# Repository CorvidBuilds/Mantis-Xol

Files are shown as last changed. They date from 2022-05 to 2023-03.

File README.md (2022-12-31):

# Hey! You should be looking at the [Armchair Engineering fork](https://github.com/Armchair-Engineering/Mantis-Xol) for the most up-to-date version!

# Mantis Xol 2


## Description
Originally a project to slap 5020 blower fans onto Mantis, this toolhead variant started as an attempt to improve parts cooling, spurred on by Derpimus' noted cooling woes on his DOOMCube. After finding that the 5020s were just plain too fat to fit without looking like a standard Ender 3 Thingiverse special, I abandoned the large fan dream in favor of better cooling efficiency and lighter weight. This new and improved dream was also corrupted by my then budding and now all-consuming love for worm gears.

## New Features for Xol 2
 - Cooler: Still a little ugly but better
 - Lighter: 260g-ish for Sherpa Mini
 - Rigid-er: I want to throw this thing across the room
 - DropEffect × Phaetus XG support 
 - Revo Voron Support
 - Support for MattTheBaker's Beacon and VoronDesign's Tap

#### Features:
 - Better airflow than Stealthburner (6-7 CFM through short ducts vs 4.6-5.2 CFM through long ducts)
 - Improved resonance management compared to Mantis 5015
 - Support for Sherpa Mini-pattern extruder mounting as well as Annex Engineering's **Double Folded Ascender** worm gear extruder
 - Support for JosAr's Klicky, VinnyCordeiro and WhoppingPochard's PCB Klicky, and Nionio6915's Euclid
 
#### Future Development (No ETA):
 - Bracing for PCB mounts
 - Quickdraw 2 support
 - Update DFA Bottom to latest version for slightly better heatset quality of life
 - Port nozzle LEDs to Xol 2
 - Port MMU sensor support to Xol 2
 - Confirm fitment for MattTheBaker's Beacon

## Build Notes:
This toolhead might require other modifications to retain full functionality of your printer. 
 - All test machines used for this mod had Rama's front idlers which have a much lower profile compared to stock Voron front idlers. The fan assemblies might conflict and reduce usable X travel.
 - The Klicky Probe carriage that was adapted was originally designed for the Dragon hotend. You'll need to use a taller probe body to reach the bed such as the one used by [Unklicky BFP](https://github.com/majarspeed/Unklicky). *This isn't an issue for Euclid or PCB Klicky*.
## Bill of Materials 
|Item|Count|Note|
|----|-|--|
|Rapido or XG|1|
|4010 24v blower fans|2|Add Polulu 3796 if you want the fancy 12v Deltas|
|2510 24v axial fan|1|
|M2x8 SHCS|2|
|M2x12 SHCS|4|
|M2x20 SHCS|2|
|M2.5x20 SHCS|4|
|m3x6 BHCS|7|
|m3x8 BHCS|7|
|m3x20 SHCS|2|
|M2 Heatset 4L x 3.5 OD|11|
|M3 Heatset "Standard"|10|
|D2F-5L Microswitch|1|
|M2x8 or M2x10 Self-Tapping|1|Optionally 1 more M2 heatset and an M2x8 SHCS|
|6x3 magnets|3|
|ZIP TIES||
## Changelog
### 29 November 2022 - Beacon Support
- Release Day means Beacon Support. Find it in the Experimental folder.
### 27 November 2022 - Tap Support
- Release Day means Tap Support. Find it in the Experimental folder.
### 22 November 2022 -Revo Voron
- Added support for Revo Voron with the Sherpa Mini Hotend mount
### 10 November 2022 - Shiny shiny
- Added nozzle LED support. Find it in the Experimental folder.
### 23 October 2022
### 3 October 2022 - Xol 2
- Improved aesthetics
- Downsized HE fan to 2510
- No more self-tapping screws
- Added front brace for Sherpa Mini
- New ducts for Tridents with lead screws
- Miscellaneous printability improvements
### 3 Aug 2022 - Xol with Boots
- Added MGN9H carriages for PCB Klicky
- Added additional stabilization for ducts. Ideally, these are fastened with 2x M2x20 and M2 heatset inserts.


## Acknowledgement
[Long/Mandryd](https://github.com/mandryd/VoronUsers/tree/master/printer_mods/Long/Mantis_Dual_5015) for the Mantis toolhead.<br/>
[TheWarolf](https://github.com/TheWarolf/Voron-Personal-Mods/tree/main/V2/Long_Mantis_Toolhead) for the ERCF sensorized Hotend Mount.<br/>
[Derpimus](https://github.com/lraithel15133) for the exegesis, some CAD work, feedback, and just being a rad dude.<br/>
[KayosMaker](https://github.com/KayosMaker) for the MGN12 Klicky X-Carriage and CAN board mounts and spacers.<br/>
[JosAr](https://github.com/jlas1/Klicky-Probe) for Klicky.<br/>
[WhoppingPochard](https://github.com/tanaes) and [VinnyCordeiro](https://github.com/VinnyCordeiro/) for PCB Klicky.<br/>
[Nionio6915](https://github.com/nionio6915/Euclid_Probe) for Euclid. <br/>
[VoronDesign](https://github.com/VoronDesign) for this particular CoreXY flavor.<br/>
[AnnexEngineering](https://github.com/Annex-Engineering) for the Sherpa Mini and Double Folded Ascender extruders, and the K3 that influenced the air management of the ducts. And also for giving access to an early revision of the new DFA so it could be adapted for this toolhead.<br/>
[Clee](https://github.com/clee), you know what you did.

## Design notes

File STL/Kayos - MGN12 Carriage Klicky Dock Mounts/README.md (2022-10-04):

The Klicky dock and mount can be found in the MantisUsermods repo [here.](https://github.com/mandryd/MantisUsermods/tree/main/Usermods/KayosMaker/MGN12_Klicky/STLs)

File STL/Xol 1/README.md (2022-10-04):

# Mantis Xol 


## Description
Originally a project to slap 5020 blower fans onto Mantis, this toolhead variant started as an attempt to improve parts cooling, spurred on by Derpimus' noted cooling woes on his DOOMCube. After finding that the 5020s were just plain too fat to fit without looking like a standard Ender 3 Thingiverse special, I abandoned the large fan dream in favor of better cooling efficiency and lighter weight. This new and improved dream was also corrupted by my then budding and now all-consuming love for worm gears.

#### Features:
 - Lighter weight (285g Sherpa Mini/300g DFA vs Stealthburner's 430g)
 - Better airflow than Stealthburner (6-7 CFM through short ducts vs 4.6-5.2 CFM through long ducts)
 - Improved resonance management compared to Mantis 5015
 - Support for Sherpa Mini-pattern extruder mounting as well as Annex Engineering's **Double Folded Ascender** worm gear extruder
 - Support for JosAr's Klicky, VinnyCordeiro and WhoppingPochard's PCB Klicky, and Nionio6915's Euclid
 - Nozzle LEDs. They're not the best but they're there.
 
#### Future Development (No ETA):
 - Bracing for PCB mounts
 - Rev 2 for ducts since the current version punishes curling too harshly and might be too low for some nozzles
 - Quickdraw 2 support
 - Update DFA Bottom to latest version for slightly better heatset quality of life
 - Revo support


## Note:
I'm not the owner of some of the STLs in this repo. The rightful owners are included in the filenames and these files will be removed in favor of a readme with links to their origin instead.
## Build Notes:
This toolhead might require other modifications to retain full functionality of your printer. 
 - Both test machines used for this mod had Rama's front idlers which have a much lower profile compared to stock Voron front idlers. The fan assemblies might conflict and reduce usable X travel.
 - The Klicky Probe carriage that was adapted was originally designed for the Dragon hotend. You'll need to use a taller probe body to reach the bed such as the one used by [Unklicky BFP](https://github.com/majarspeed/Unklicky). *This isn't an issue for Euclid or PCB Klicky*.
## Bill of Materials 
|Item|Count|Note|
|----|-|--|
|4010 24v blower fans|2|Add Polulu 3796 if you want the fancy 12v Deltas|
|3010 24v axial fan|1|
|M2x8 or M2x10 self-tapping|12|
|Rapido|1|
|m3x20 SHCS|2|
|m3x12 BHCS|2|
|m3x6 BHCS|6|
|6x3 magnets|3|
|Heatset|4|
|D2F-5L Microswitch|1|
|ZIP TIES||
|||
|**Optional**||
|**Nozzle LEDs**||
|SB nozzle LED kit or 2 of the spec RGB/RGBW LED chips||
|**Toolhead board**||
|HartK board v4 or CAN 36|
|Heatset|4|
|**Sensorized Mount**||
|D2F-5L Microswitch|1|
|M2x8 or M2x10 self-tapping|2|
|7mm Steel ball|1|
|**With Boots**||
|M2x20 SHCS|2|
|M2 Heatset Insert|2|https://www.amazon.com/gp/product/B08ZN4PS65|
## Changelog
### ?? September 2022 - Xol 2
- Improved aesthetics
- Downsized HE fan to 2510
- No more self-tapping screws
- Added front brace for Sherpa Mini
- New ducts for Tridents with lead screws
### 3 Aug 2022 - Xol with Boots
- Added MGN9H carriages for PCB Klicky
- Added additional stabilization for ducts. Ideally, these are fastened with 2x M2x20 and M2 heatset inserts.


## Acknowledgement
[Long/Mandryd](https://github.com/mandryd/VoronUsers/tree/master/printer_mods/Long/Mantis_Dual_5015) for the Mantis toolhead.<br/>
[TheWarolf](https://github.com/TheWarolf/Voron-Personal-Mods/tree/main/V2/Long_Mantis_Toolhead) for the ERCF sensorized Hotend Mount.<br/>
[Derpimus](https://github.com/lraithel15133) for the exegesis, some CAD work, and feedback.<br/>
[KayosMaker](https://github.com/KayosMaker) for the MGN12 Klicky X-Carriage and CAN board mounts and spacers.<br/>
[JosAr](https://github.com/jlas1/Klicky-Probe) for Klicky.<br/>
[WhoppingPochard](https://github.com/tanaes) and [VinnyCordeiro](https://github.com/VinnyCordeiro/) for PCB Klicky.<br/>
[Nionio6915](https://github.com/nionio6915/Euclid_Probe) for Euclid. <br/>
[VoronDesign](https://github.com/VoronDesign) for this particular CoreXY flavor.<br/>
[AnnexEngineering](https://github.com/Annex-Engineering) for the Sherpa Mini and Double Folded Ascender extruders, and the K3 that influenced the air management of the ducts. And also for giving access to an early revision of the new DFA so it could be adapted for this toolhead.<br/>
[Clee](https://github.com/clee), you know what you did.

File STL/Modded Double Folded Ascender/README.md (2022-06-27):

# License Notice
Because this STL is derived from an Annex Engineering design, it is bound by their license.

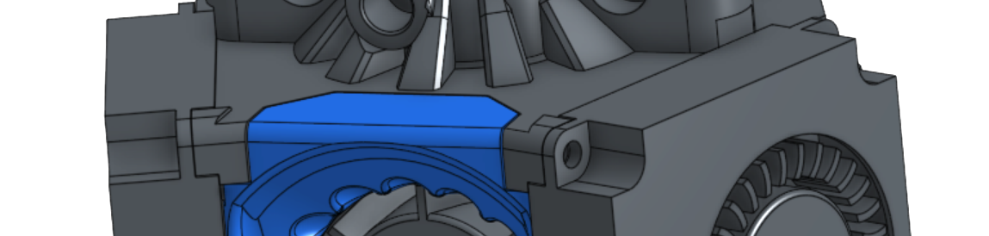
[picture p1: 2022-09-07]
Images/Xol2Preview.png

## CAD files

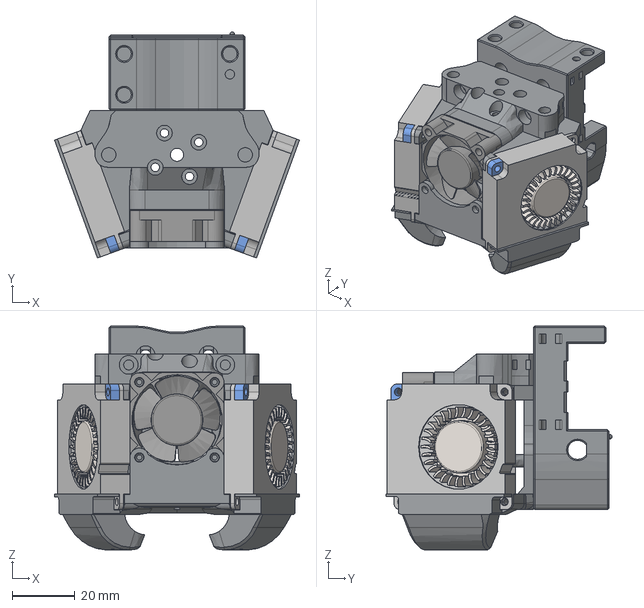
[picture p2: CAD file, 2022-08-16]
CAD/Xol 1/Mantis Xol - Sherpa Mini.step
78.1 x 72.1 x 71.3 mm

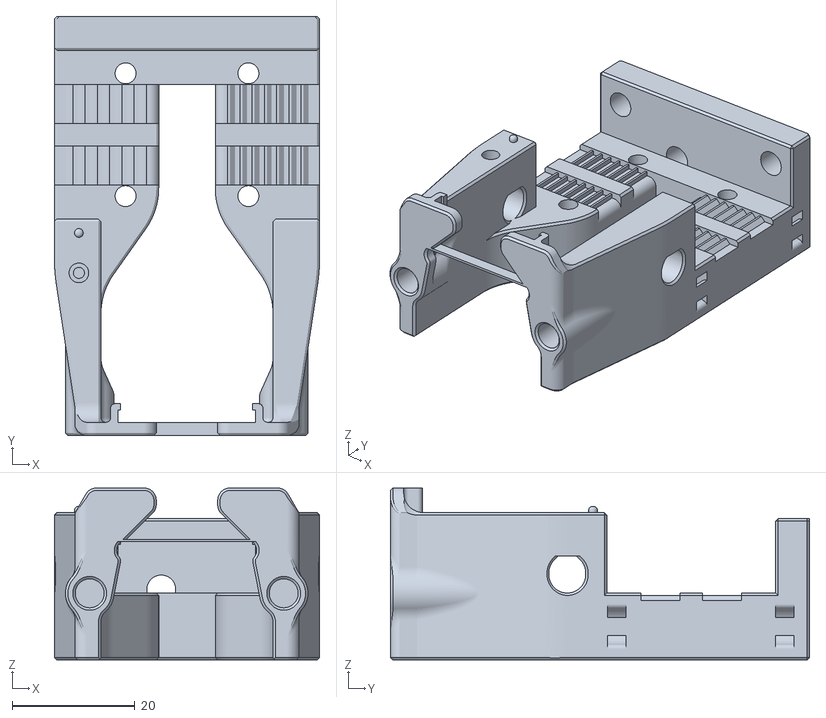
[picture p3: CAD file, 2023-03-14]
STL/Carriage/DFA/Mantis Xol DFA - Carriage - MGN12 Beacon - HS Endstop.stl
43.2 x 68.2 x 28.0

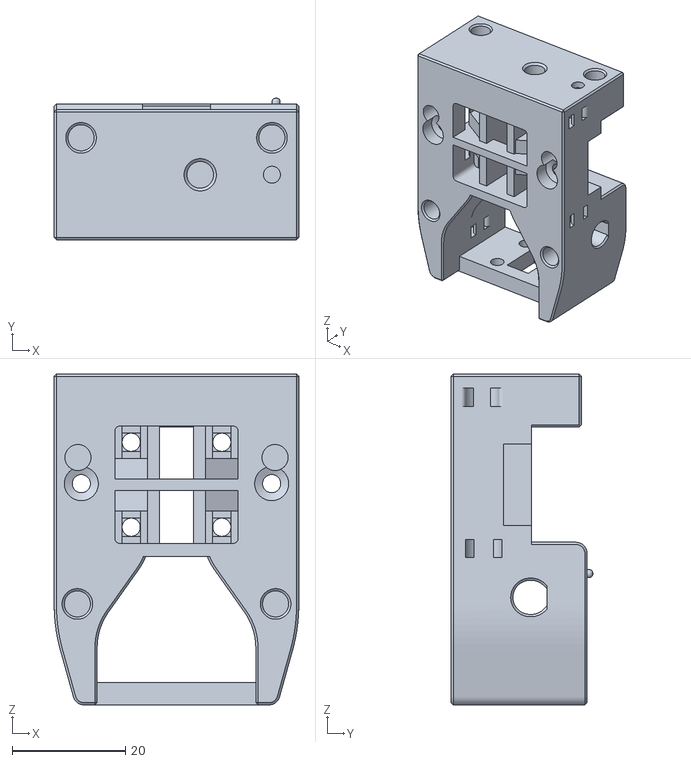
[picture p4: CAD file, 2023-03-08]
STL/Experimental/Mantis Xol DFA - Carriage - MGN9H PCB Klicky - HS Endstop.stl
43.2 x 25.0 x 58.4

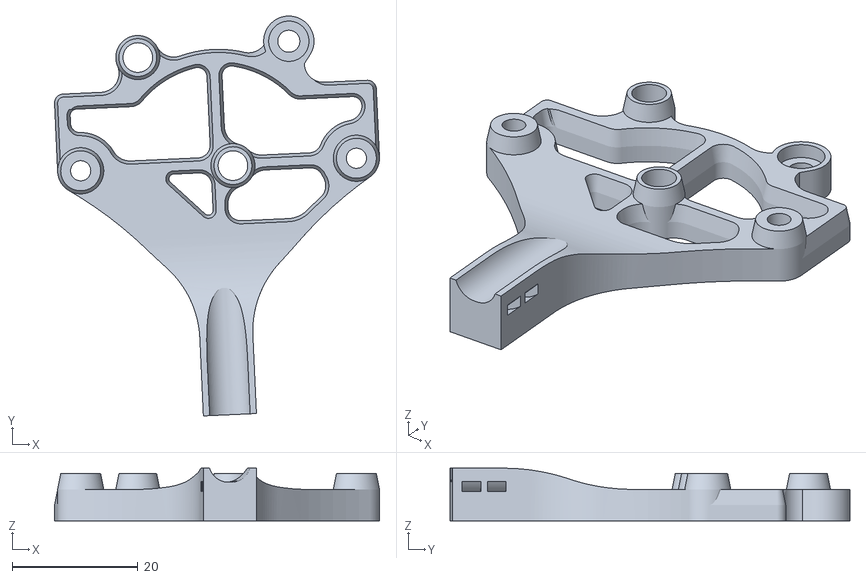
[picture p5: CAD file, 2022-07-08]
STL/Hartk PCB Mount/[a]_Mantis Xol - DFA - Hartk3_mounting_plate_strain_relief.stl
51.6 x 63.5 x 8.36

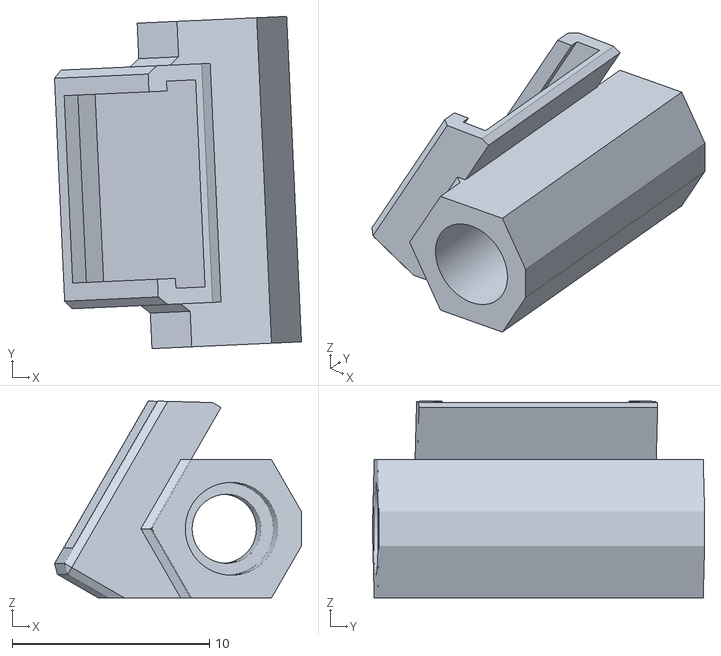
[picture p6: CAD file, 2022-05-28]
STL/Hartk PCB Mount/Motor Spacers/17mm motor/Mantis Xol - Polulu 3796 Mount - 16.5mm.stl
12.5 x 16.8 x 9.97

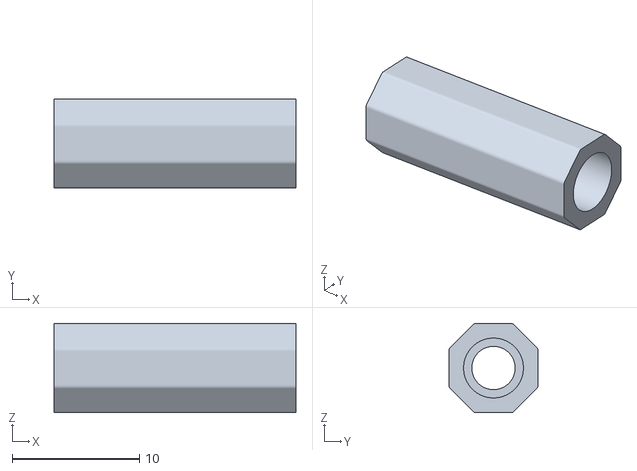
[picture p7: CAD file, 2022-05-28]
STL/Hartk PCB Mount/Motor Spacers/20mm motor/Kayos - 19.0mm_hex_universal_spacer.stl
19.0 x 7.00 x 7.00

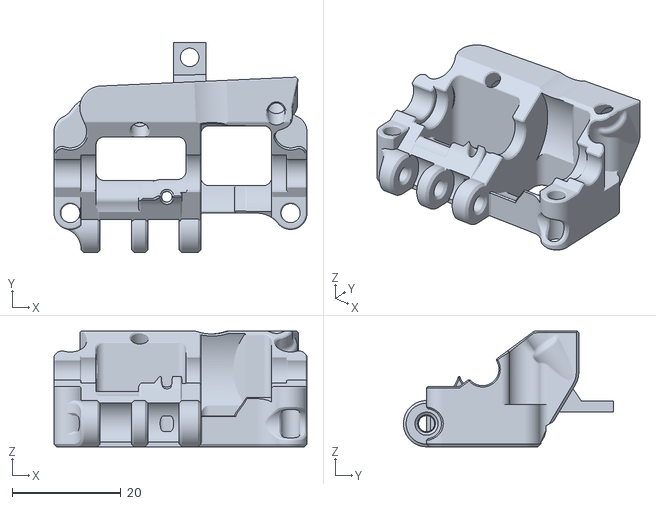
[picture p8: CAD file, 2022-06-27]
STL/Modded Double Folded Ascender/Mantis_Xol - DFA Bottom.stl
46.5 x 38.6 x 21.2

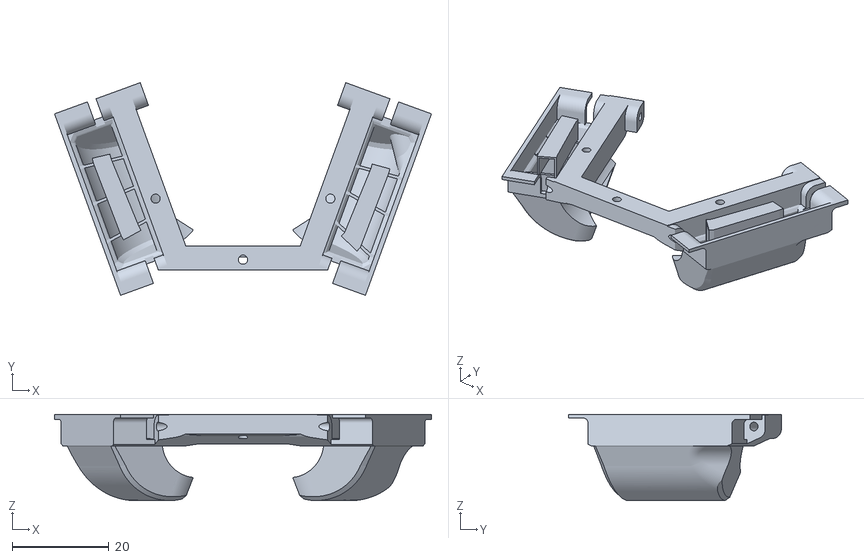
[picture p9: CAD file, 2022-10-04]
STL/Xol 1/Mantis Xol - Ducts - Tri-Vane Asym Trident.stl
78.1 x 44.1 x 17.8

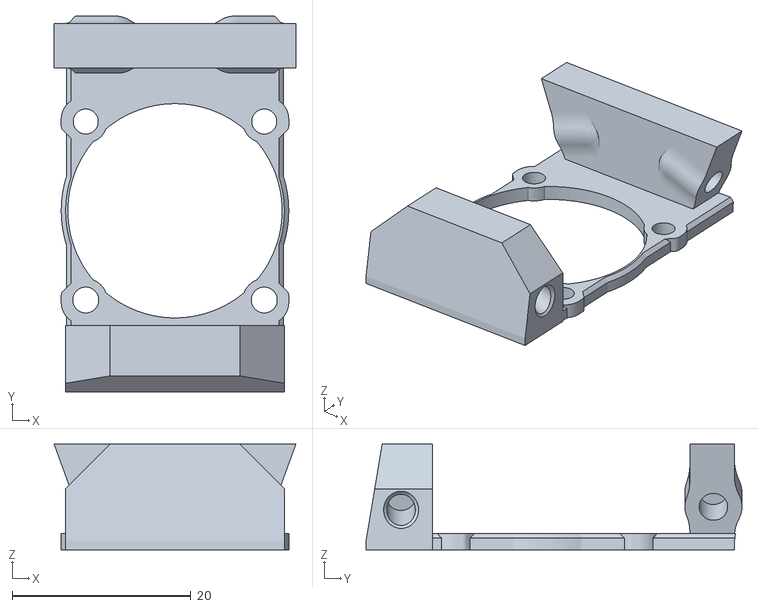
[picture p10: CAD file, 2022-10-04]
STL/Xol 2/Rapido/[a]_Xol 2 Rapido - Faceplate B.stl
27.1 x 42.1 x 11.8

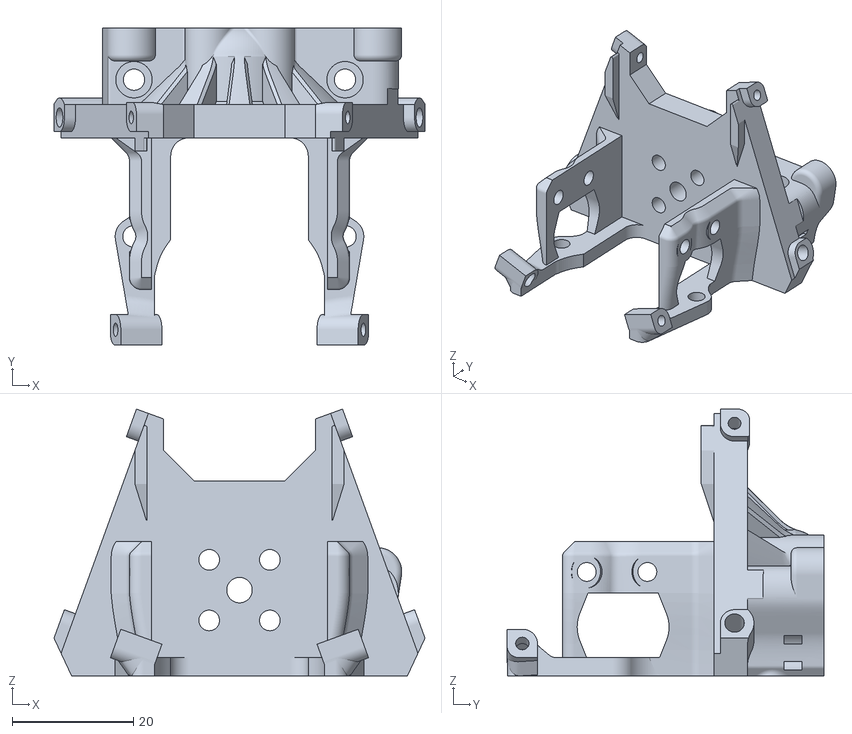
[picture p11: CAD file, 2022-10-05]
STL/Xol 2/XG/Xol 2 XG - Hotend Mount - DFA.stl
61.2 x 52.2 x 44.0

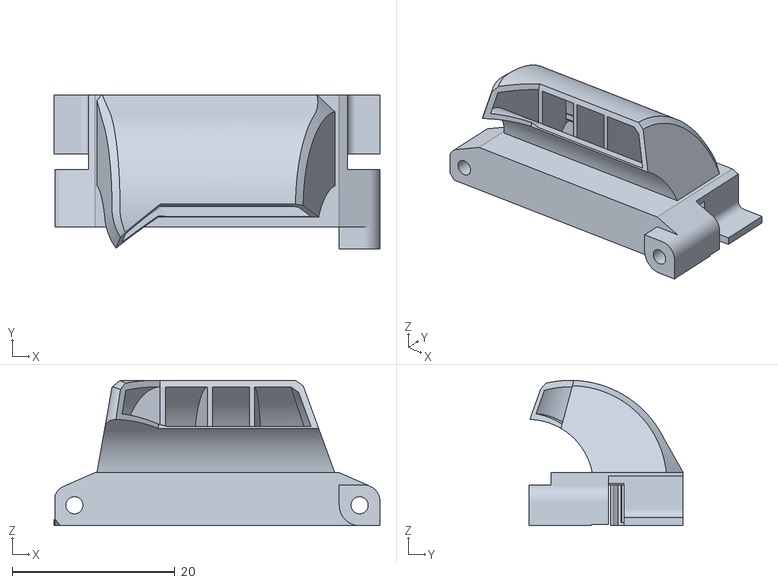
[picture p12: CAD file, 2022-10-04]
STL/Xol 2/Xol 2 - Ducts - Tri-Vane Asym B.stl
40.0 x 18.9 x 17.8

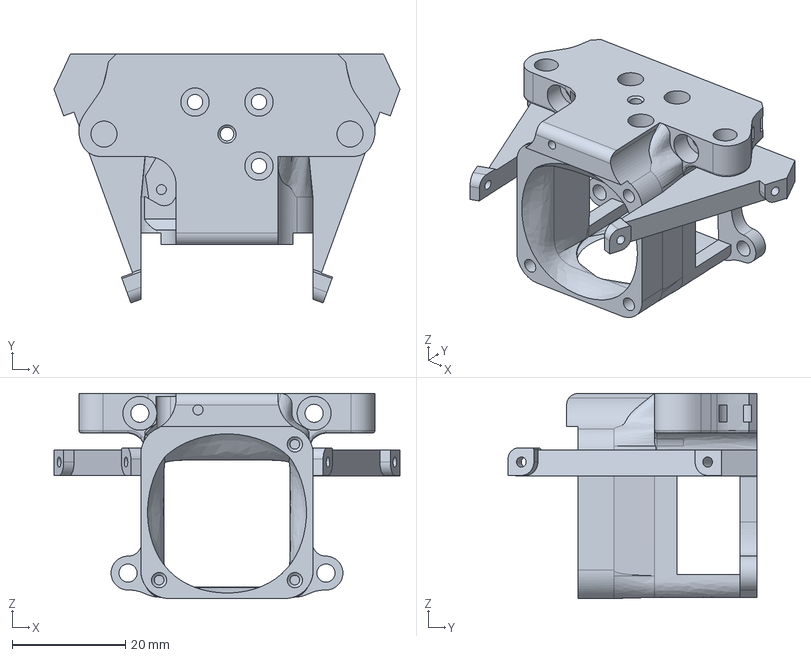
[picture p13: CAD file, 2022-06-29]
CAD/Xol 1/Mantis Xol - Hotend_MountERCF.step
61.2 x 44.0 x 36.3 mm

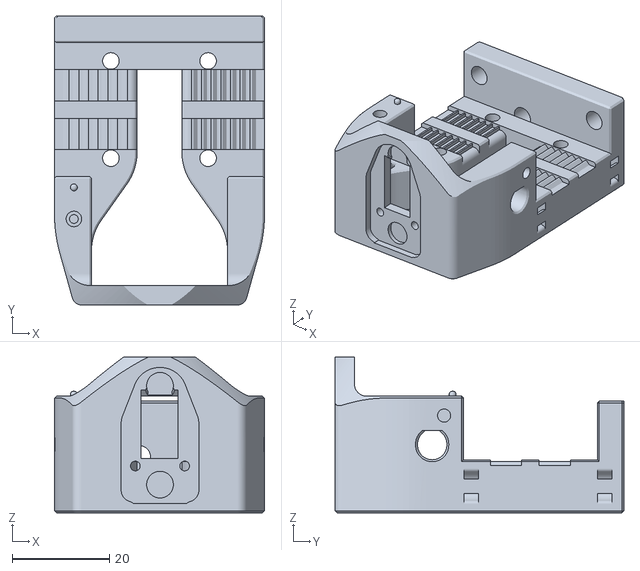
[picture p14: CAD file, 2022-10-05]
STL/Carriage/DFA/Mantis Xol DFA - Carriage - MGN12 Euclid - HS Endstop.stl
43.2 x 59.4 x 32.0

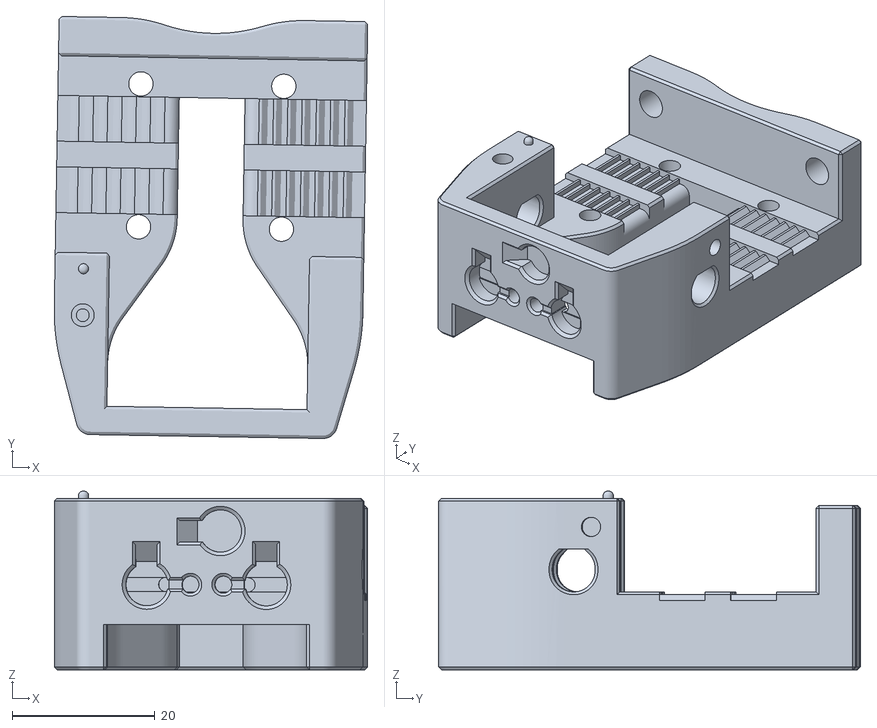
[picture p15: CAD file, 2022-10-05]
STL/Carriage/Sherpa/Mantis Xol Sherpa - Carriage - MGN12 Klicky - HS Endstop.stl
43.9 x 59.1 x 25.0

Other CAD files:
STL/Carriage/Sherpa/Mantis Xol Sherpa - Carriage - MGN12 Beacon - HS Endstop.stl
STL/Experimental/Xol 2 - Duct UHF A - Tri-Vane .stl
STL/Hartk PCB Mount/[a]_Mantis Xol - DFA - PCB Mount Stabilizer.stl
STL/Hartk PCB Mount/Motor Spacers/17mm motor/Kayos - 16.5mm_hex_universal_spacer.stl
STL/Carriage/DFA/Mantis Xol DFA - Carriage - MGN12 Euclid.stl
STL/Carriage/DFA/Mantis Xol DFA - Carriage - MGN12 Klicky - HS Endstop.stl
STL/Carriage/DFA/Mantis Xol DFA - Carriage - MGN12 Klicky.stl
STL/Carriage/DFA/Mantis Xol DFA - Carriage - MGN12 PCB Klicky - HS Endstop.stl
STL/Carriage/DFA/Mantis Xol DFA - Carriage - MGN12 PCB Klicky.stl
STL/Carriage/Sherpa/Mantis Xol Sherpa - Carriage - MGN12 Euclid - HS Endstop.stl
STL/Carriage/Sherpa/Mantis Xol Sherpa - Carriage - MGN12 Euclid.stl
STL/Carriage/Sherpa/Mantis Xol Sherpa - Carriage - MGN12 Klicky.stl
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

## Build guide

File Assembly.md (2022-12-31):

# Assembly of YOUR NEW Mantis Xol 2 Toolhead

| Instruction | |
| --- | --- |
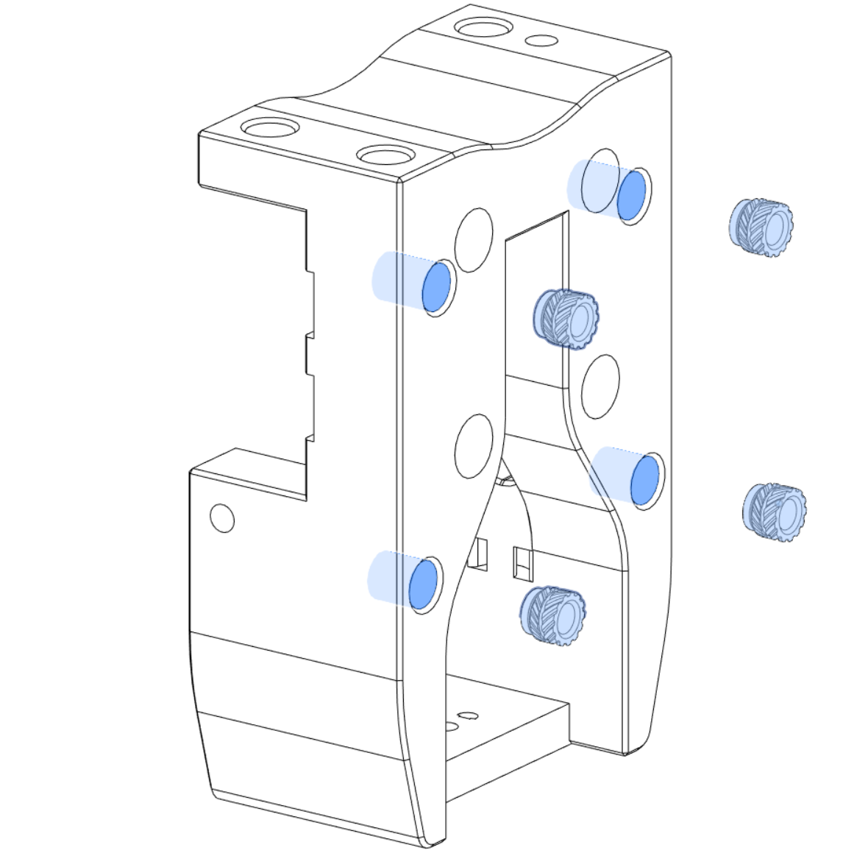
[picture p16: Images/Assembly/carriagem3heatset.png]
Carriage M3 Heatsets
| Insert **M3** Heatset Inserts into the *Carriage* as indicated. For best results, insert almost completely with a soldering iron before finishing by pressing against a flat, heat resistant surface. |   |
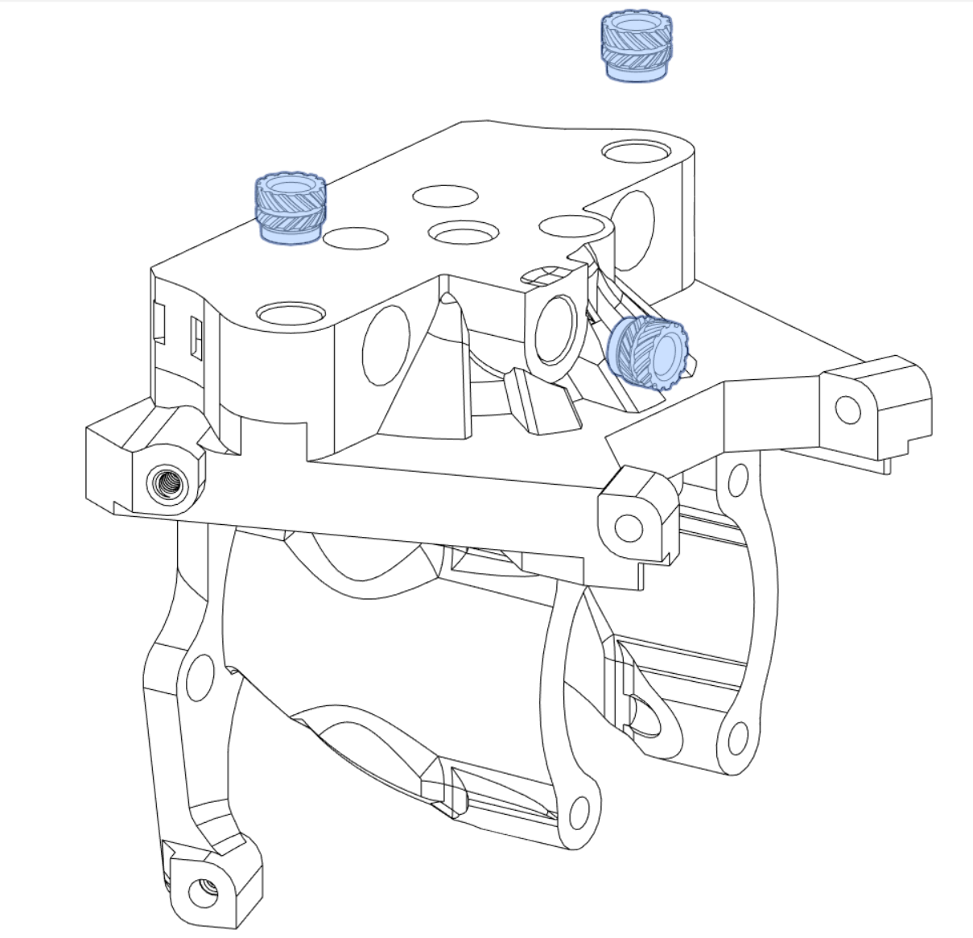
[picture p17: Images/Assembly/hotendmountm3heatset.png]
Hotend Mount M3 Heatsets
| Insert **M3** Heatset Inserts into the *Hotend Mount* as indicated. Judicious use of the tip mentioned in the previous step will be helpful. |   |
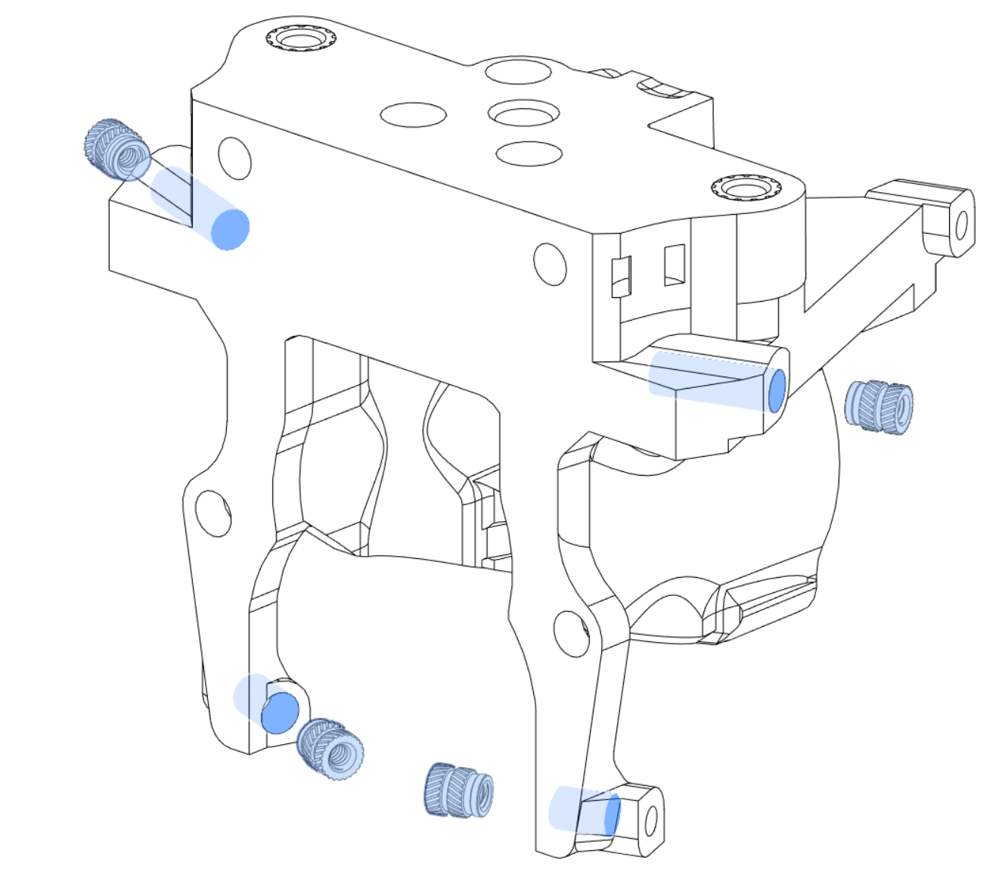
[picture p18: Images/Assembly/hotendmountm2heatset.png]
Hotend Mount M2 Heatsets
| Insert **M2** Heatset Inserts into the *Hotend Mount* as indicated. For the upper Heatset Inserts, you may use the table method if you're careful not to deform the plastic. For the lower Heatset Inserts, this is less recommended. You may use one of the M2x20s to ream the holes in Xol's boots as the displaced plastic may now act as an obstruction in a later step. |    |
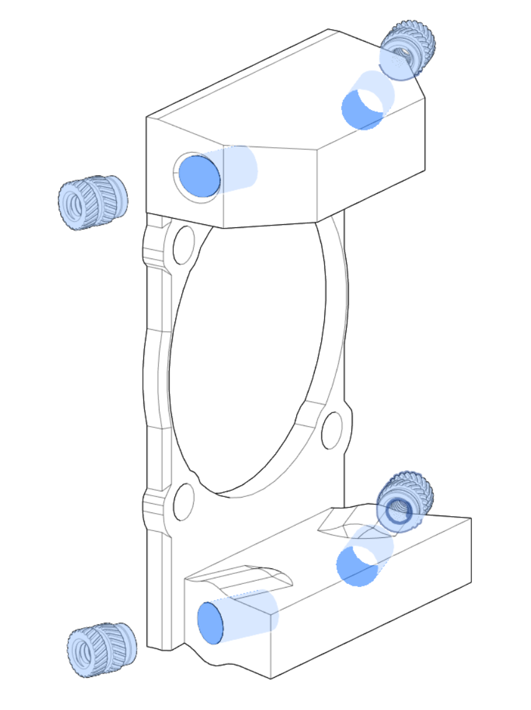
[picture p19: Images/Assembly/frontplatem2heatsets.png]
Front Plate M2 Heatsets
| Insert **M2** Heatset Inserts into the faceplate as indicated. **Note:** The upper Heatset Inserts here are not flat against the plastic part. Attempting to use the flat surface tip mentioned in previous steps will ruin your day. Do your best to make the upper Heatset Inserts parallel to the lower. |    |
| Prepare the wiring for the Z probe of your choice. Follow instructions for your specific selection as provided in that solution's repo. The Heatset Insert tip may or may not be helpful during this step. | This image space left intentionally blank.  |
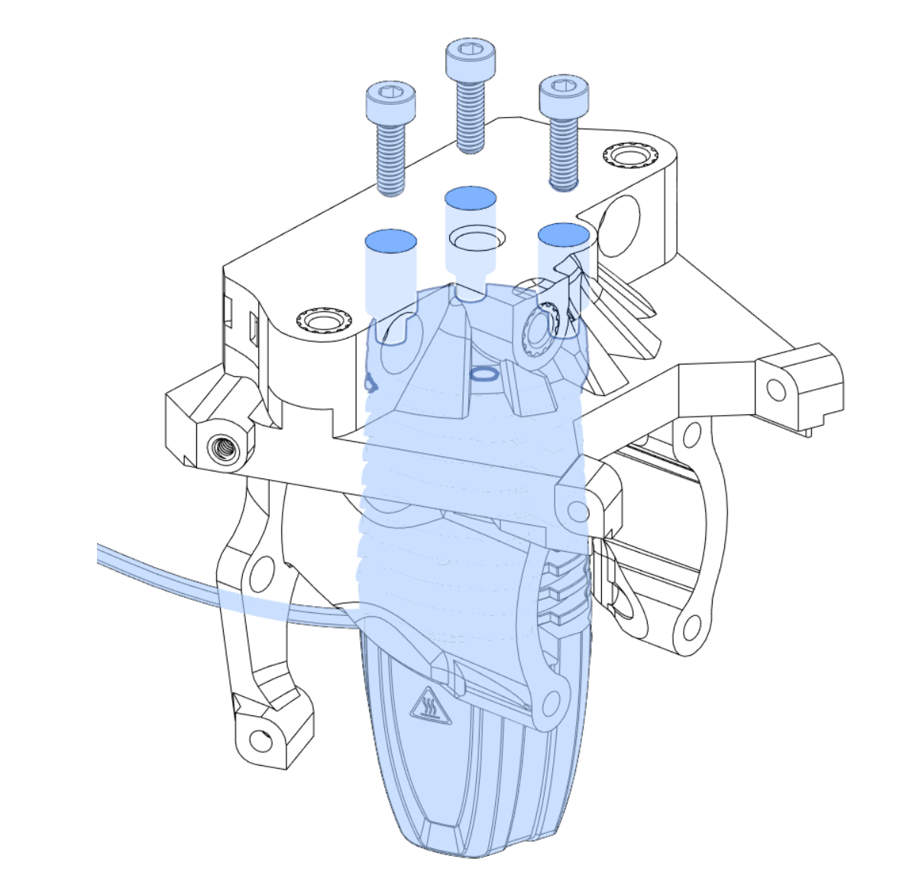
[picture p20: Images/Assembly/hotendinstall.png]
Hotend Install
| Attach your hotend of choice (Rapido shown here) using the corresponding screws for your selection. For Rapido, ensure that your heater and thermistor wiring exit toward the rear left. There is no application for the aforementioned Heatset Insert tip during this step. |   |
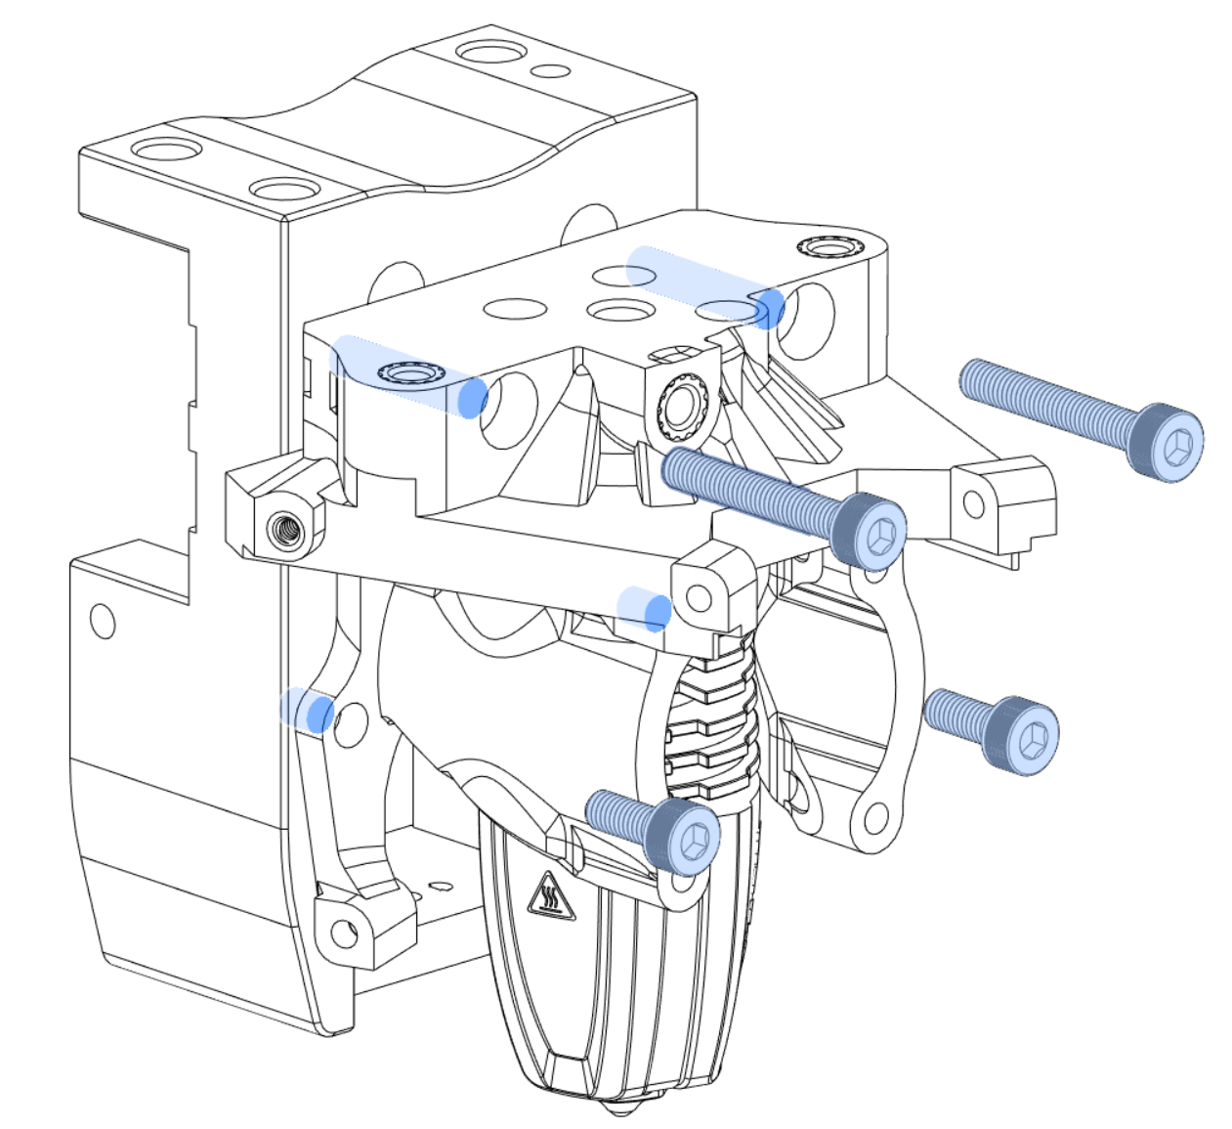
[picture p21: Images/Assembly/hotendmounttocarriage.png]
Hotend Mount to Carriage
| Attach the *Hotend Mount* to the *Carriage* as indicated, using M3X20 screws in the upper positions and M3x8 in the lower. **Note:** Don't crush your wiring. |   |
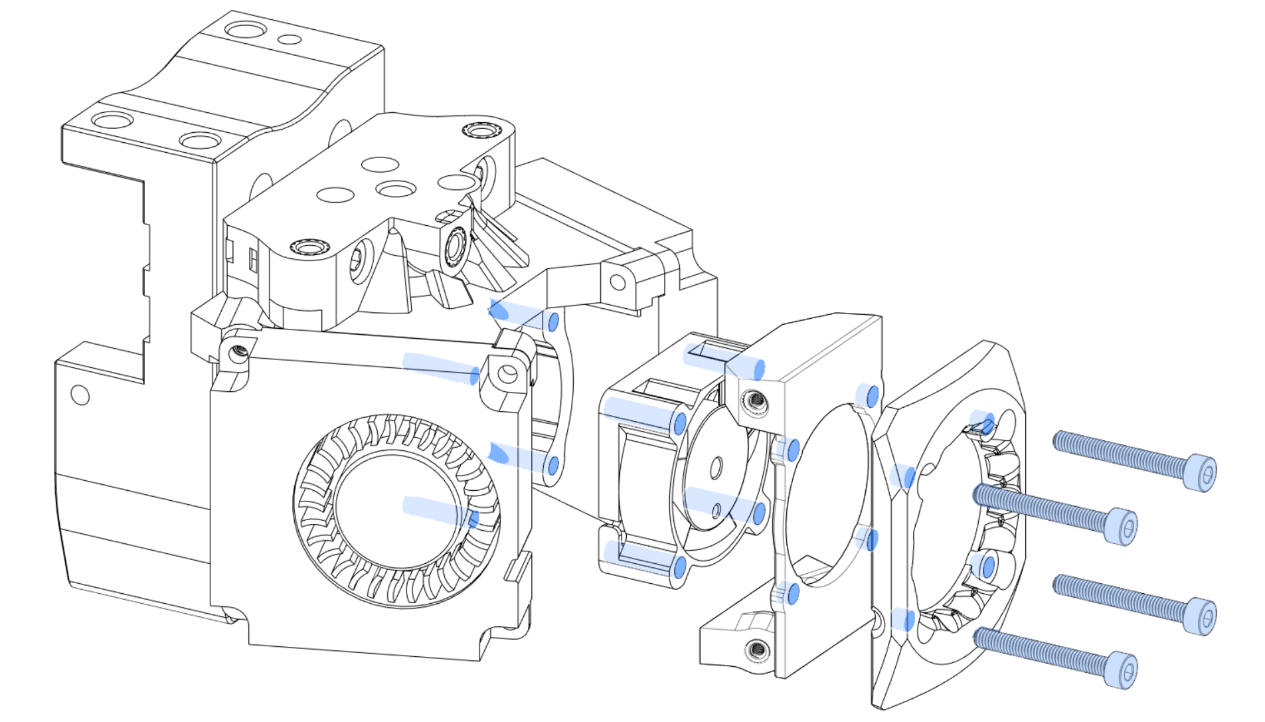
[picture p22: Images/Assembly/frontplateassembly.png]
Front Plate Assembly
| Fasten the *Faceplate* and *2510 Hotend Fan* to the *Hotend Mount* with M2.5x20 screws as indicated. For XG, there will only be 2. Ensure that the *Hotend Fan* wiring exits toward the left as indicated. |  |
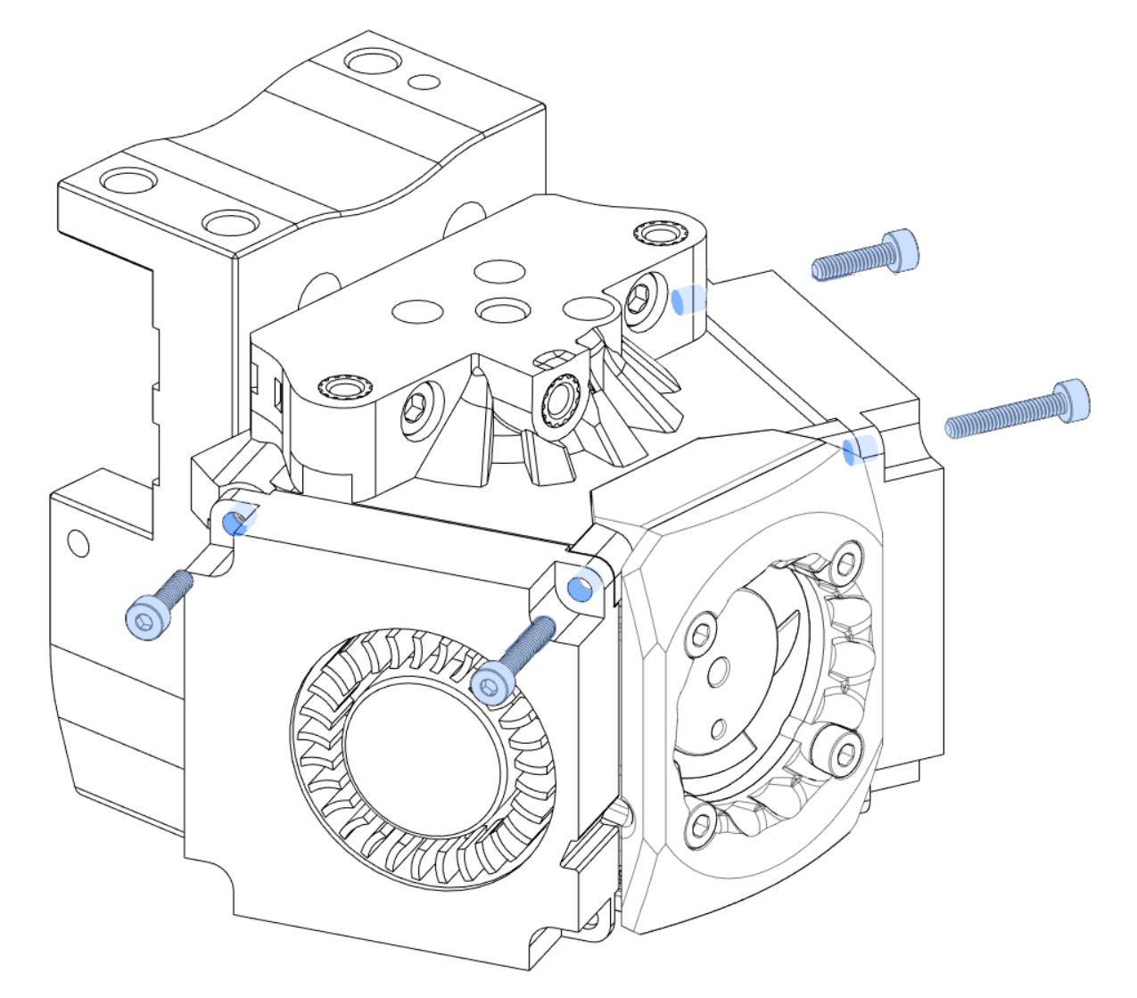
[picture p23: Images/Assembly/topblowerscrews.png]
Top Blower Screws
| Fasten the *4010 Parts Cooling Fans* to the *Hotend Mount* as indicated using M2x8 in the rear and M2x12 in the front.  |   |
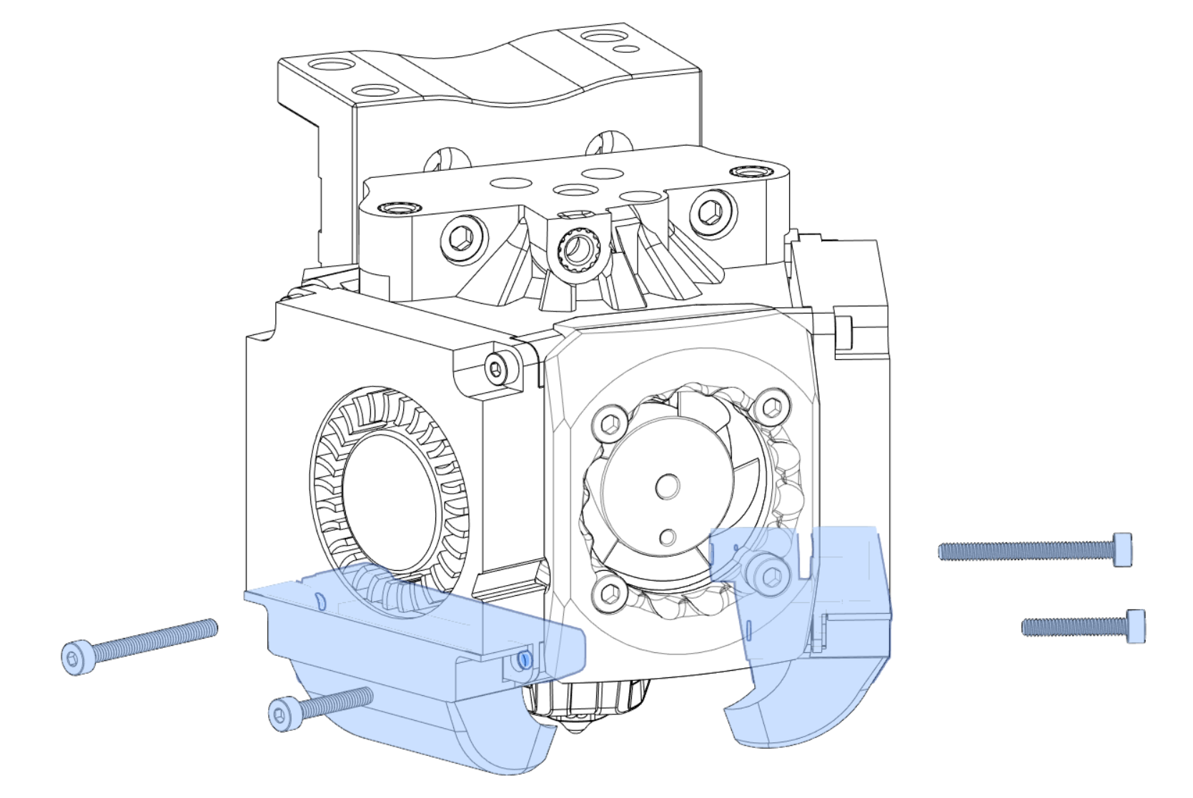
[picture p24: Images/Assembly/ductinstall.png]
Bottom Blower Screws and Duct Install
| Fasten the *4010 Parts Cooling Fans* and attach *Ducts* as indicated using M2x20 in the rear and M2x12 in the front.  |   |
| Attach your selected *Extruder* with corresponding PTFE.  | This image space left intentionally blank.  |
| Secure your wiring with zipties.  | This image space left intentionally blank.  |
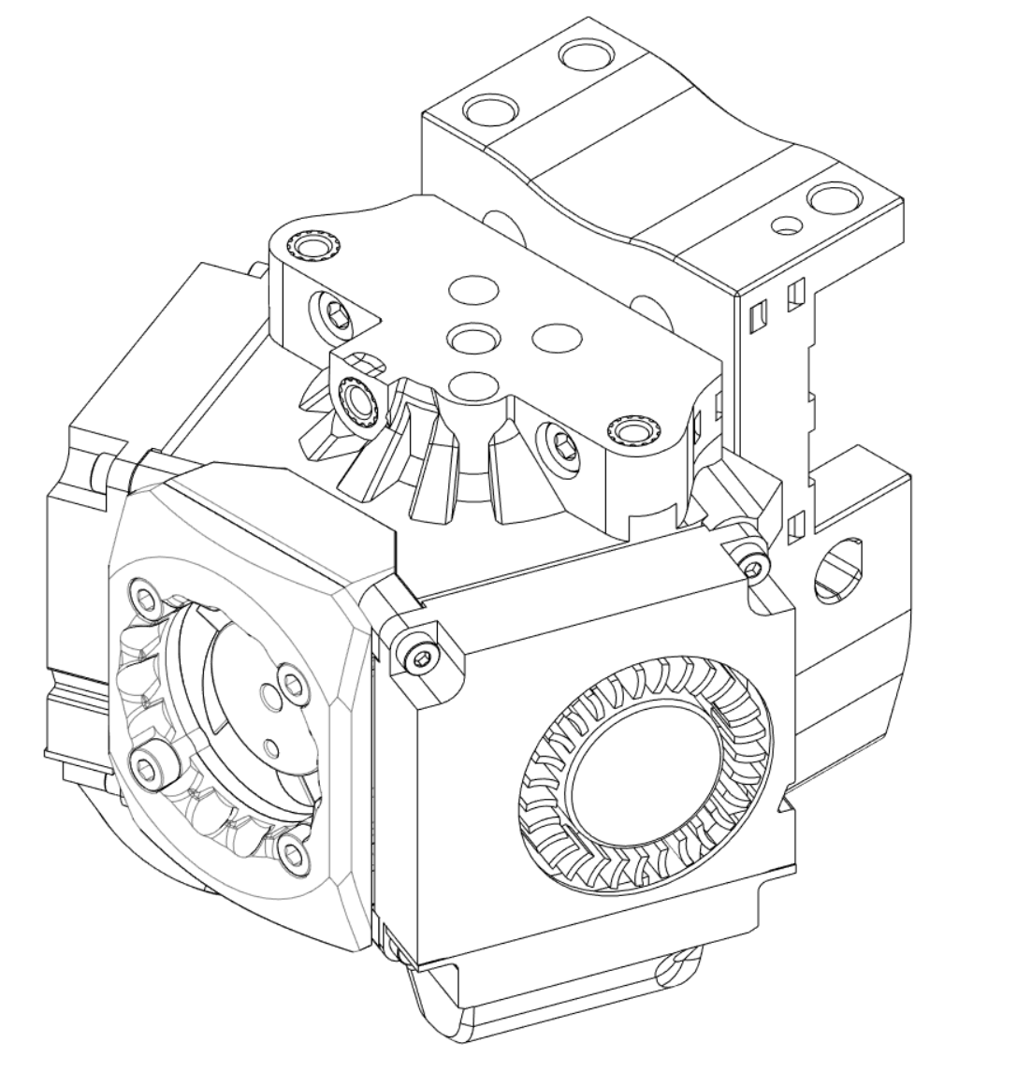
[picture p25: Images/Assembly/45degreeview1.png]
45 Degree Preview
| You're done! Congratulations!  |   |

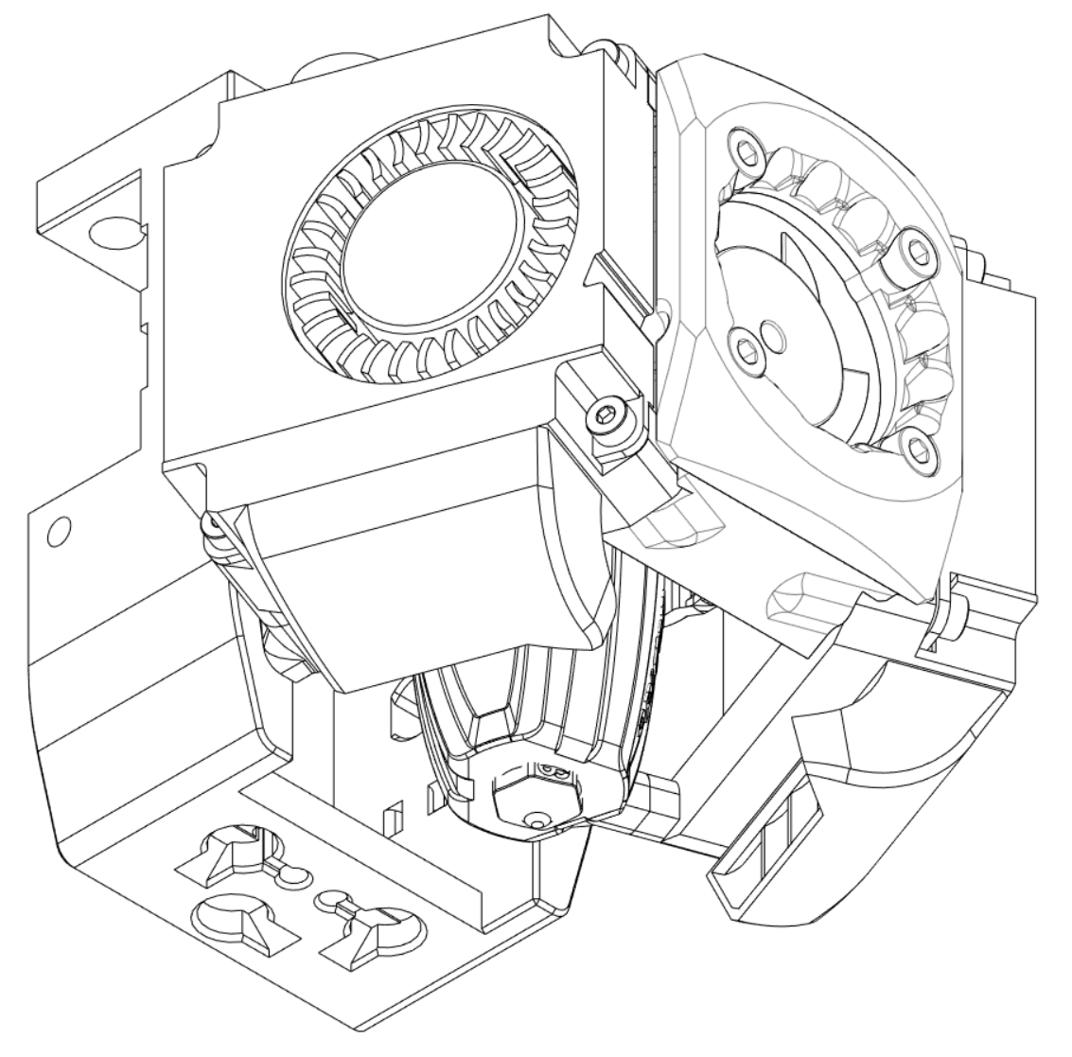
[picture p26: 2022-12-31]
Images/Assembly/45degreeview2.png

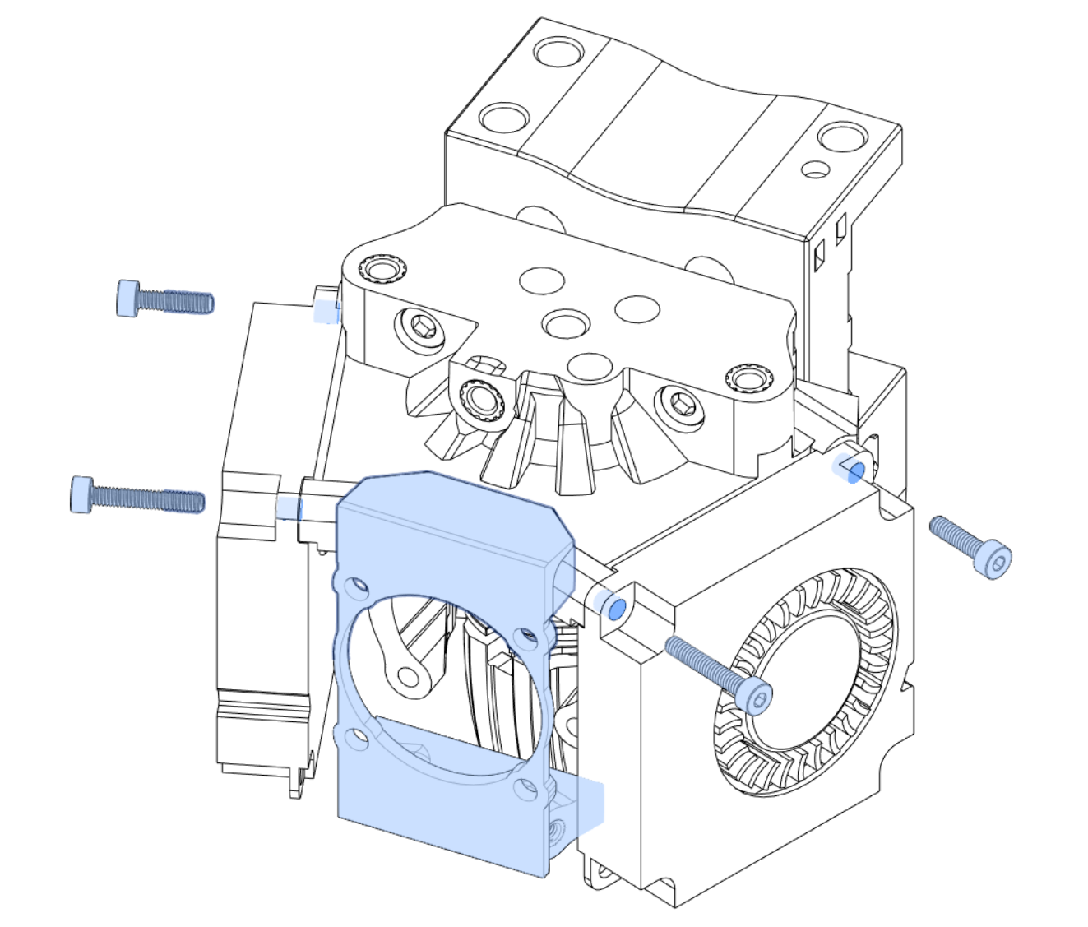
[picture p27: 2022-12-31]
Images/Assembly/frontplateandfaninstall.png

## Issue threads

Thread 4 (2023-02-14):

CAN boards

erazor666, 2023-02-14:
What if any CAN boards can be used with this, I wanna try this toolehead very much but having built CANbus and umbilical I'm never going back to wires ever again.

CorvidBuilds, 2023-02-14:
Any NEMA14 pancake CAN boards work with the Sherpa Mini or DFA versions by using mounts found here:
https://github.com/KayosMaker/CANboard_Mounts

I recommend using brass standoffs instead of printed parts.

Closed 2023-02-14.

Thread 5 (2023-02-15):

Rapido support

erazor666, 2023-02-15:
By Rapido is it the Standard or UHF model we are talking about? Any other/modified fan ducts needed for the UHF version?

CorvidBuilds, 2023-02-15:
Rapido HF is standard for Xol and Xol 2. However, there are UHF ducts for both in the Experimental folder. Note that if you decide to use UHF, you may have to modify your Z probing solution. There are people who have done this but I am not one.

Closed 2023-02-15.

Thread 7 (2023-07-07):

Mantis Xol DFA - MGN12 Carriage HS - Beacon.stl dont fit with the rapido mount

Fragmon, 2023-07-07:
Hello,

i would use the XOL2 with a Beacon but the holes from the mount and the carriage dont fit. The distance between the holes are not the same.

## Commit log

2022-05-28 Alpha test upload
    [Dock_sidemount_fixed_v2.stl, Hotend_MountERCF.step, Kayos - 19.0mm_hex_universal_spacer.stl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]
2022-05-29 Create Mantis 4010 - Ducts - Tri-Vane - Beta 2 Asym.stl
    [Mantis 4010 - Ducts - Tri-Vane - Beta 2 Asym.stl]
2022-06-08 Moved HE fan 2mm closer, incorporated duct brace brace
    [Mantis 4010 - Ducts - Tri-Vane - Beta 3 Asym.stl, Mantis 4010 - Face Plate - Beta.stl, Mantis 4010 - LED Carrier - Beta.stl]
2022-06-08 Update Mantis 4010 - Hotend Mount+ERCF - Rapido.stl
2022-06-27 DFA Release package
    [Mantis_Xol - DFA Bottom.stl]
2022-06-29 Add updated CAD assemblies
    [Mantis Xol - Sherpa Mini.step]
2022-06-29 Updated ERCF Hotend Mount version
    Should ask Derp if he edited this after he got it
    [Hotend_MountERCF.step, Mantis Xol - Hotend_MountERCF.step]
2022-06-29 Added PCB Klicky, updated naming
    [Mantis Xol DFA - Carriage - MGN12 Klicky.stl, Mantis Xol DFA - Carriage - PCB Klicky.stl, Mantis Xol Sherpa - Carriage - MGN12 Klicky.stl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]
2022-06-30 More updating formats, removing old versions of stuff,
    [Mantis 4010 - Ducts - Tri-Vane - Beta 2 Asym.stl, Mantis 4010 - Ducts - Tri-Vane - Beta.stl, Mantis Xol - Ducts - Tri-Vane Asym.stl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]
2022-06-30 Carriage STLs got tired and are taking a nap
    [Mantis Xol DFA - Carriage - MGN12 PCB Klicky.stl, Mantis Xol DFA - Carriage - PCB Klicky.stl, Mantis Xol Sherpa - Carriage - MGN12 PCB Klicky.stl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]
2022-07-03 UHF ducts and readme roadmap
    [UNTESTED Mantis Xol - Ducts UHF - Tri-Vane Asym.stl]
2022-07-08 Added Euclid and DFA PCB stabilizer
    [Mantis Xol DFA - Carriage - MGN12 Euclid.stl, Mantis Xol Sherpa - Carriage - MGN12 Euclid.stl, [a]_Mantis Xol - DFA - Hartk3_mounting_plate_strain_relief.stl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]
2022-08-04 Xol with Boots
    [Mantis Xol DFA - Carriage - MGN9H PCB Klicky.stl, Mantis Xol Sherpa - Carriage - MGN9H PCB Klicky.stl]
2022-08-04 MGN9H Euclid
    [Mantis Xol DFA - Carriage - MGN9H Euclid.stl, Mantis Xol Sherpa - Carriage - MGN9H Euclid.stl]
2022-08-16 Updating CAD assemblies with boots
    [Mantis Xol - Sherpa Mini.step]
2022-09-07 Improve printability for Euclid carriage
    [Mantis Xol DFA - Carriage - MGN12 Euclid.stl]
2022-10-04 Xol 2 release?
    [Dock_sidemount_fixed_v2.stl, Mantis Xol - Ducts - Tri-Vane Asym Trident.stl, Mantis Xol - Ducts - Tri-Vane Asym.stl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]
2022-10-05 Heatset X Endstop on MGN12, DFA Hotend mount printability improvement, readme
    [Mantis Xol DFA - Carriage - MGN12 Euclid - HS Endstop.stl, Mantis Xol DFA - Carriage - MGN12 Klicky - HS Endstop.stl, Mantis Xol DFA - Carriage - MGN12 PCB Kli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]
2022-10-05 Oriented new STLs
    [Mantis Xol DFA - Carriage - MGN12 Euclid - HS Endstop.stl, Mantis Xol DFA - Carriage - MGN12 Klicky - HS Endstop.stl, Mantis Xol DFA - Carriage - MGN12 PCB Kli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]
2022-10-23 Updated CAD
    [Mantis Xol - Hotend_MountERCF.step, Mantis Xol - Sherpa Mini.step]
2022-11-10 Added Nozzle LED to Experimental because it is
    [Xol 2 - LED Holder.stl, Xol 2 Rapido - Faceplate w LED.stl]
2022-11-29 :bacon: but without missing faces, I think
    [Mantis Xol DFA - MGN12 Carriage HS - Beacon.stl]
2022-12-18 MGN9 Beacon + Xol 2 UHF Duct
    [Mantis Xol Sherpa - MGN9 Carriage - Beacon.stl, Xol 2 - Duct UHF A - Tri-Vane .stl, Xol 2 - Duct UHF B - Tri-Vane.stl]
2022-12-31 Assembly instructions
2023-03-08 Mid-cycle refresh
    [Mantis Xol DFA - Carriage - MGN9H Euclid.stl, Mantis Xol DFA - Carriage - MGN9H PCB Klicky - HS Endstop.stl, Mantis Xol DFA - Carriage - MGN9H PCB Klicky.stl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]
2023-03-14 :bacon: Carriages
    [Mantis Xol DFA - Carriage - MGN12 Beacon - HS Endstop.stl, Mantis Xol Sherpa - Carriage - MGN12 Beacon - HS Endstop.stl]
